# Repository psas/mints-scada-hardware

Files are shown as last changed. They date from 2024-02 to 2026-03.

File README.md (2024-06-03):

# mints-scada-hardware
Minimal Test Stand Supervisory Control and Data Acquisition system hardware and firmware. See [mints-scada-software](https://github.com/psas/mints-scada-software) for the computer software to control the whole system. 

# Assembly
### stm32devboards
* Populate all SMD components on the board
    * Only populate the 60.4 ohm CAN termination resistors on the nodes on the ends of the chain.
    * Populate the USB port and solder its mounting lugs
    * Do not populate the headers on the sides as they will make it more difficult to work on the boards if problems are discovered
* Complete the board testing
* Populate THT components
### interface-module
* Select the desired configuration of the board. This can be one of
    * 8x Push and/or Pull outputs
    * 4x I2C
    * 4x ADC
    * See notes in KiCad for configuration information
* Assemble only the required components for that version of the board. Leave the rest unpopulated

# Firmware flashing
Firmware files are located in the `firmware/bin` directory.

### Command line (recommended)
Command line firmware flashing instructions are provided for Ubuntu 24.04. Other debian-based Linux distros should follow a similar procedure. Flashing from Mac or Windows should be possible, but is not covered here.
#### Setup
1. Install `dfu-util` with `sudo apt install dfu-util`
2. Set up udev rules
    1. Put the following into `/etc/udev/rules.d/60-stm32`
    ```
    # STM32
    ACTION=="add", SUBSYSTEM=="usb", ATTRS{idVendor}=="0483", ATTRS{idProduct}=="df11", TAG+="uaccess"
    ```
    2. Either reboot or run `sudo udevadm control --reload-rules && sudo udevadm trigger` to reload the udev rules

#### Flashing:
1. Remove the devboard from the module if it was installed.
2. Put the device in bootloader mode
    * If the device is unplugged, hold the `BOOT` button while plugging it in
    * If the device is already plugged in, press `RESET` and `BOOT`, then release `RESET` then `BOOT`
3. Run `dfu-util --list` and confirm that there are two devices with the vendor:product ID `0483:df11`, one with the name `@Option Bytes` and one with the name `@Internal Flash`. If any other devices with that ID are present, remove them before continuing.
4. Flash the device with `dfu-util --device 0483:df11 --alt 0 --dfuse-address 0x08000000:leave --download [path/to/file/]<filename>.bin`. It should erase the flash, then download the new file and show `File downloaded successfully` when it is done.

### Visual
[STM32CubeProgrammer](https://www.st.com/en/development-tools/stm32cubeprog.html) can be used to flash device firmware. Setup will be platform-dependent, and thusly not covered here.

To build and upload:
1. Open the PlatformIO tab in the left toolbar
2. Under `PROJECT TASKS` > `Build` > `General` execute the `Build` procedure by clicking on it
3. Execute `Upload` to upload to the microcontroller. Ensure that only a single board is plugged in to ensure you are writing to the correct device.

# Building Firmware
Building firmware from source shouldn't be needed unless you are making changes to it. Firmware build instructions are provided for Ubuntu 24.04. Other debian-based Linux distros should follow a similar procedure. Flashing from Mac or Windows should be possible, but is not covered here.

You will need:
* GCC for arm `sudo apt install gcc-arm-none-eabi`
* make `sudo apt install make`
* Everything as described in the command line flashing setup section above.

To build the code, simply run `make` in the firmware folder. This will build the firmware and copy the .bin into the firmware folder. Running `make flash` will build the firmware then upload it to a connected DFU mode microcontroller.

Initialization code was generated using [https://www.st.com/en/development-tools/stm32cubemx.html](STM32Cube initialization code generator). You should not need to mofidy this, but if you do, the `module_io.ioc` is included. If you regenerate the code, you may have to add
```
#######################################
# Flash
#######################################
flash: all
	dfu-util --device 0483:df11 --alt 0 --dfuse-address 0x08000000:leave --download $(BUILD_DIR)/$(TARGET).bin
```
to the end of `Makefile`. Optionally, add `cp $(BUILD_DIR)/$(TARGET).bin $(TARGET).bin` to target `all` in the makefile (add line 171) to copy the bin out of the build direcotry. Generally, CubeMX does not seem to update the Makefile if it exists.

# Testing
### stm32devboards
1. Populate all SMD components as described in the `assembly` sections. Do not populate THT components yet
2. Visually inspect the board. Fix any issues and inspect again until no issues remain
    * Verify that no pins are shorted
    * Verify the correct orientation and alignment of all components. Pay special attention to the STM32 since its square shape makes it more difficult to notice errors
    * Bridges can hide under the USB port where you can't see them unless you tilt the board to look deep under the port. They can often be fixed by applying flux then heating the two bridged pins.
    * Fixing any of these issues is easier before soldering THT parts since everything here is reflow safe, so it is less likely to be damaged during repairs.
3. Use a DMM to test between `GND` `3v3`, and `GND` and either pad of the polyfuse (the component in the corner of the board by the USB port). Verify there are no shorts.
4. On your computer run `sudo dmesg -Hw` to monitor system messages in real time (`-m`) with human-readable timestamps (`-h`). Keep this window open and visible for the next step
5. Plug the board in via USB. Watch `dmesg`. The following should appear. If it does not, then there is a problem with your board.
```
[<starttime>] usb 3-2: new full-speed USB device number <id> using xhci_hcd
[  +0.148877] usb 3-2: New USB device found, idVendor=0483, idProduct=df11, bcdDevice=22.00
[  +0.000014] usb 3-2: New USB device strings: Mfr=1, Product=2, SerialNumber=3
[  +0.000006] usb 3-2: Product: STM32  BOOTLOADER
[  +0.000006] usb 3-2: Manufacturer: STMicroelectronics
[  +0.000005] usb 3-2: SerialNumber: FFFFFFFEFFFF
```
6. Use the above procedure to flash the `blink-fast.bin` firmware. Confirm that the LED blinks at about 10Hz.
7. Use the above procedure to flash the `blink-slow.bin` firmware. Confirm that the LED blinks at about 1Hz. This confirms that you are able to flash new firmware to the device.
8. Install the THT components as described in the assembly section.

`blink-fast.bin` and `blink-slow.bin` should already be built in the `firmware/bin` directory. If they are not, they can be rebuilt with the blink project. To rebuild them, run the following in `firmware/blink`
```
make clean && make DELAY=500 && cp blink.bin ../bin/blink-slow.bin
make clean && make DELAY=50 && cp blink.bin ../bin/blink-fast.bin
```

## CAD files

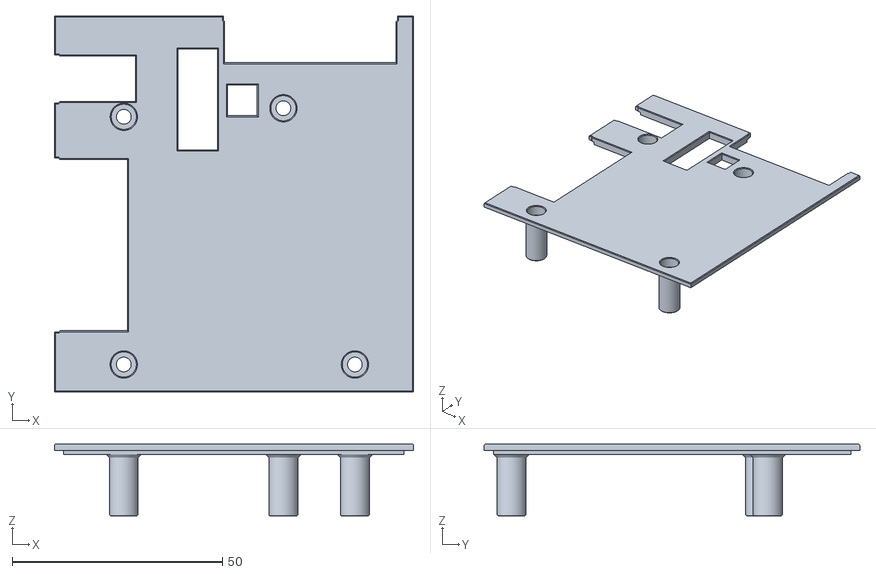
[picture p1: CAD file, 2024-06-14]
interface-module/boxes/minTS Dev Box - Lid - Outputs - v1.7.2.stl
85.5 x 89.5 x 17.1

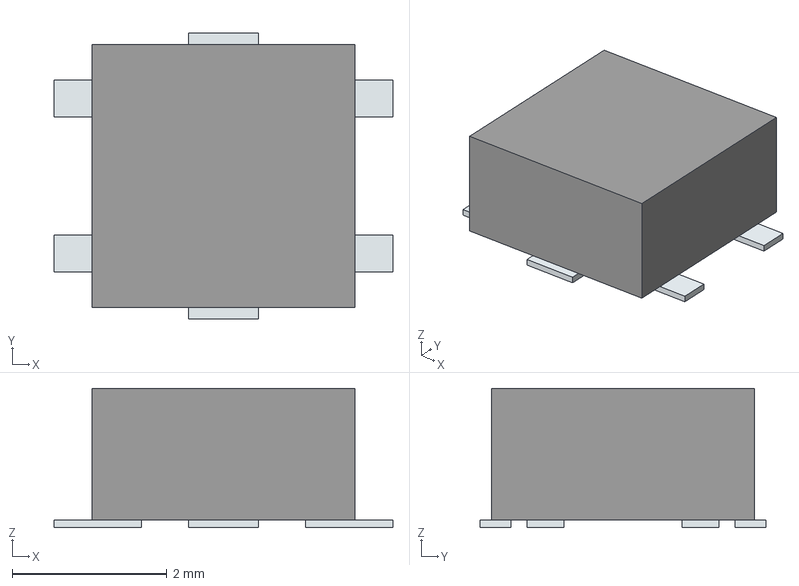
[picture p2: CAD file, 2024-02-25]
stm32devboard/3d/TS21-34-035-BK-260-SMT-TR.stp
4.38 x 3.70 x 1.80 mm
Pins

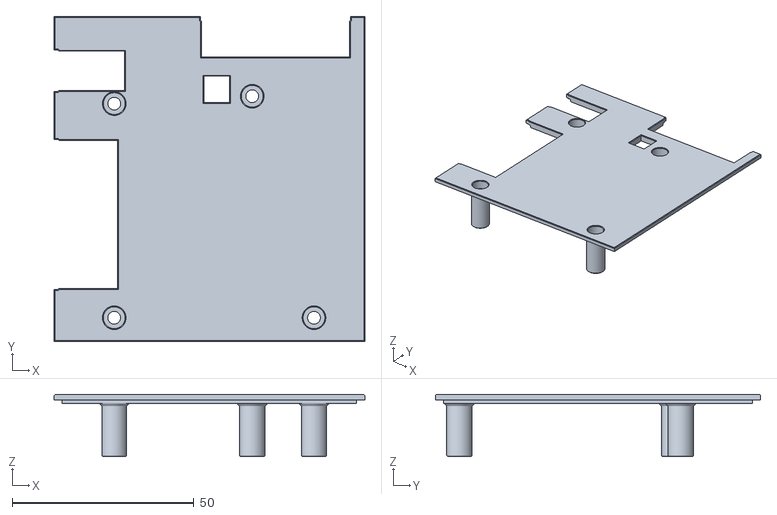
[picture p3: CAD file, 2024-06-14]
interface-module/boxes/minTS Dev Box - Lid - I2C - v1.7.2.stl
85.5 x 89.5 x 17.1

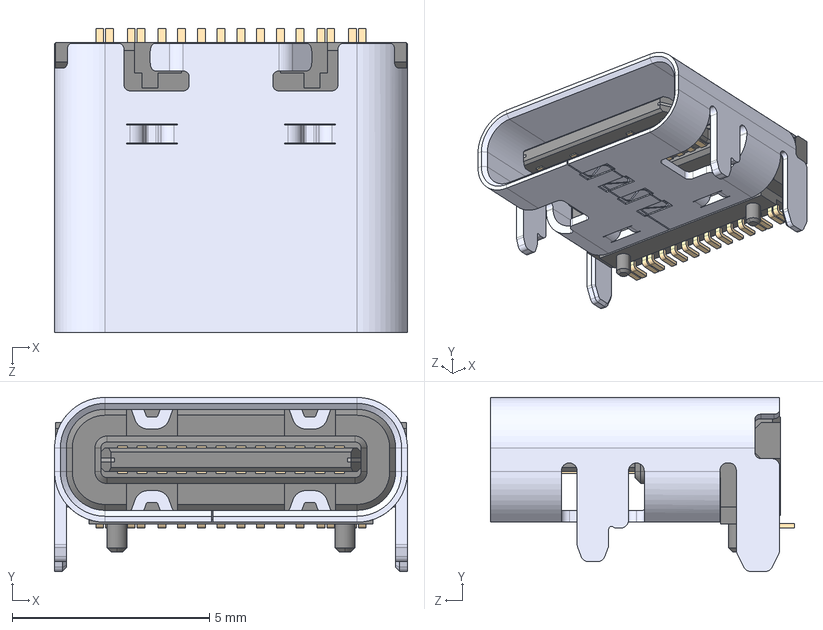
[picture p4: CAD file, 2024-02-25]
stm32devboard/3d/USB4105-GF-A.step
8.94 x 4.41 x 7.71 mm

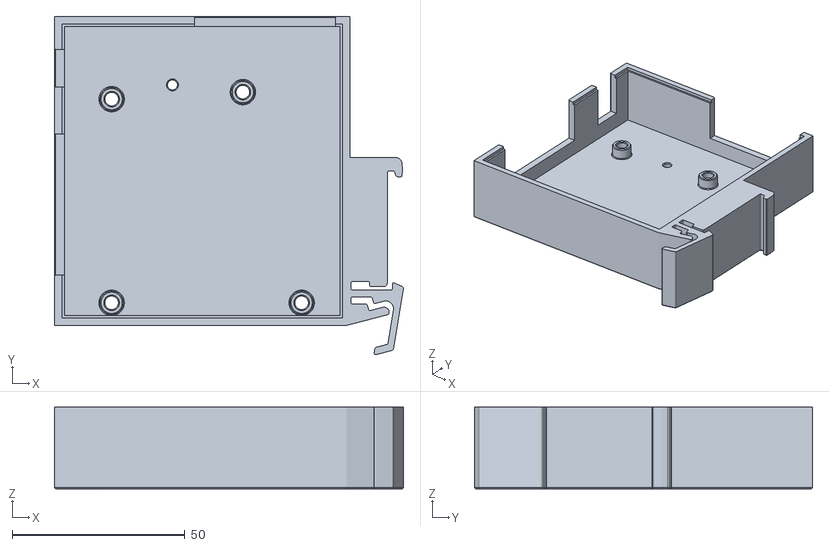
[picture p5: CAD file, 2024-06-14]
interface-module/boxes/minTS Dev Box - Bottom - v1.7.2.stl
101.0 x 97.9 x 23.6

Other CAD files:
interface-module/boxes/minTS Dev Box - Lid - ADC - v1.7.2.stl

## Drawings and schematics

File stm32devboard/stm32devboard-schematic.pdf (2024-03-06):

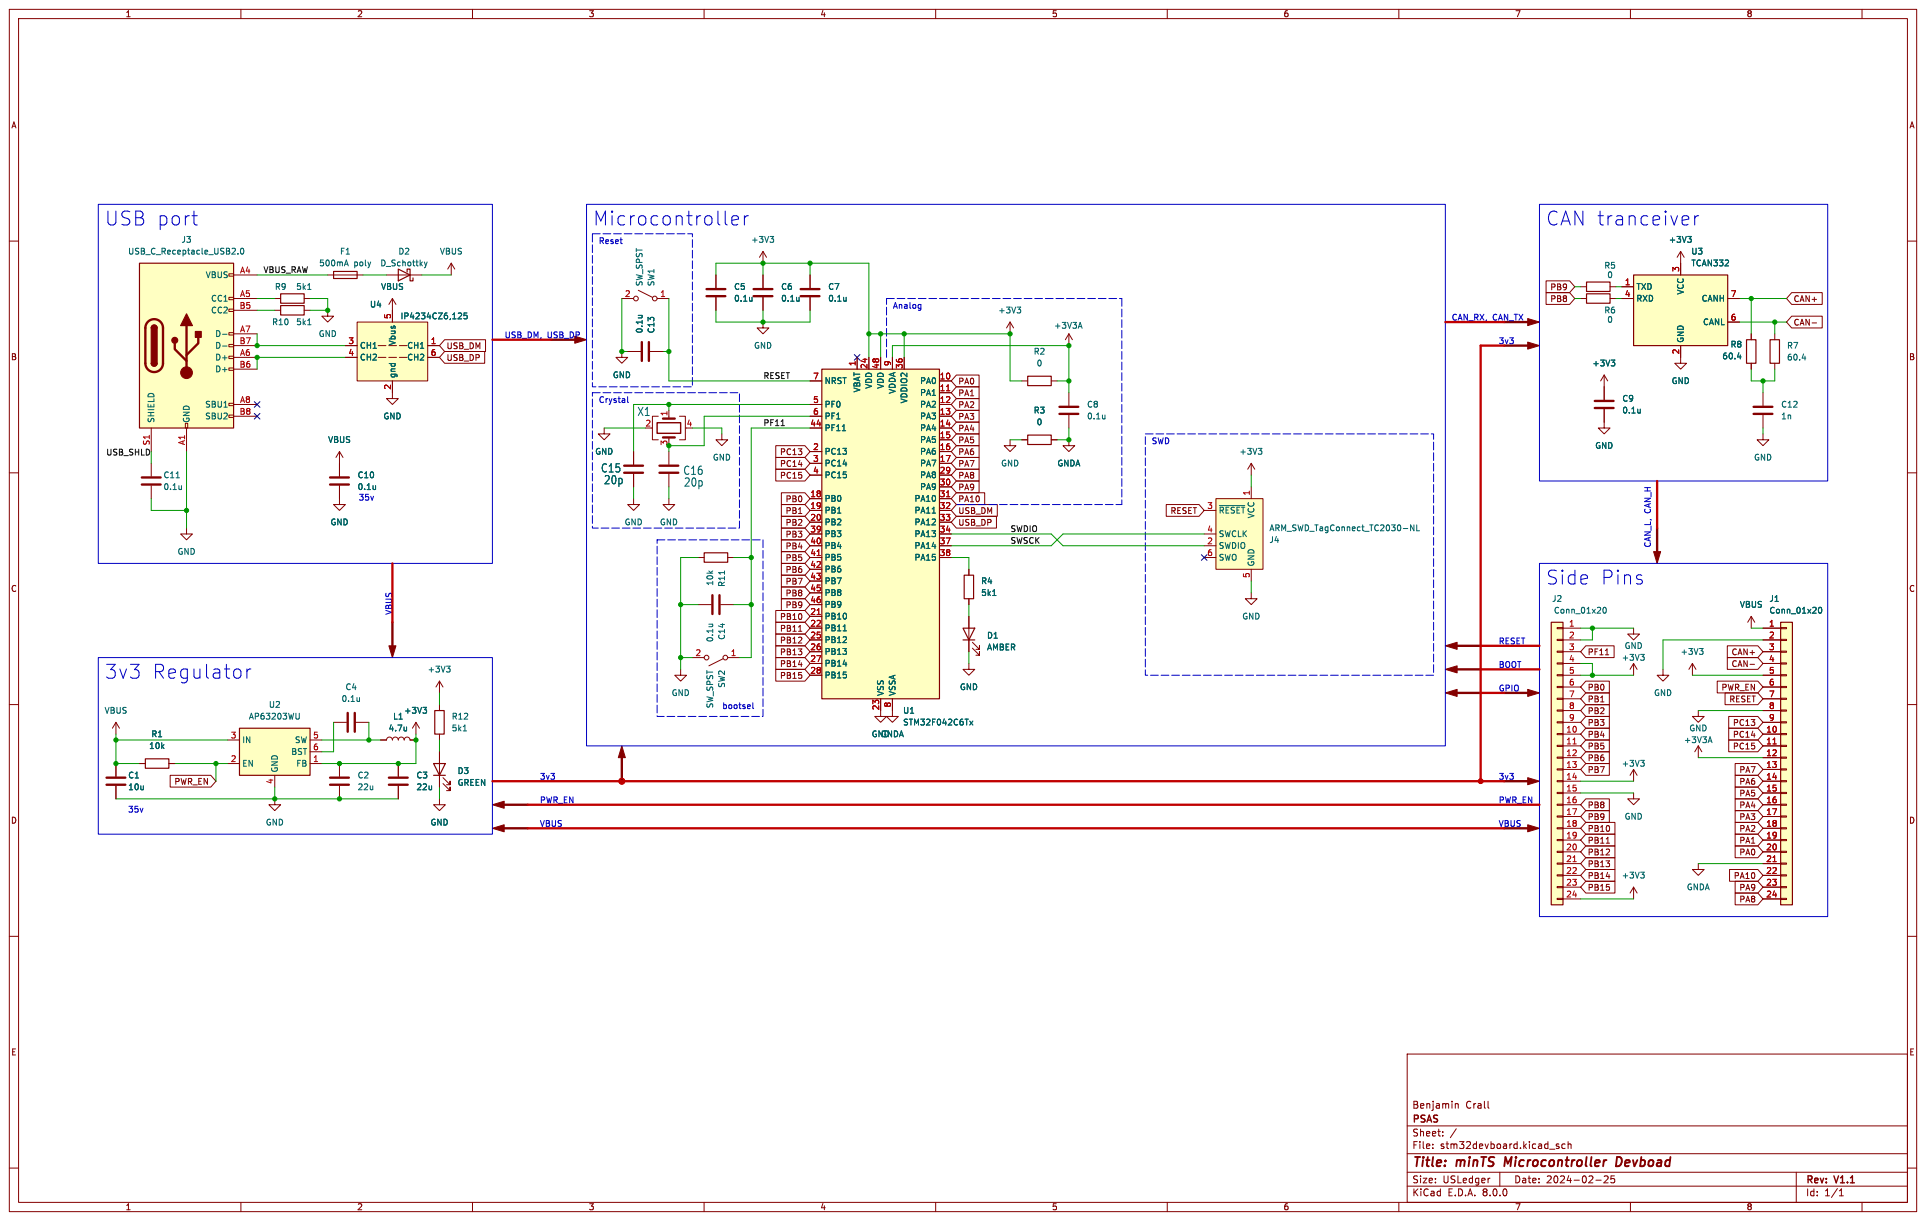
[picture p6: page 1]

1 PA0 10 PA1 11 PA2 12 PA3 13 PA4 14 PA5 15 PA6 16 PA7 17 PB0 18 PB1 19 PC13 2 PB2 20 PB10 21 PB11 22 VSS 23 VDD 24 PB12 25 PB13 26 PB14 27 PB15 28 PA8 29 PC14 3 PA9 30 PA10 31 PA11 32 PA12 33 PA13 34 VDDIO2 36 PA14 37 PA15 38 PB3 39 PC15 4 PB4 40 PB5 41 PB6 42 PB7 43 PF11 44 PB8 45 PB9 46 VDD 48 PF0 5 PF1 6 NRST 7 VSSA

1 SWDIO 2 ~{RESET} 3 SWCLK 4 GND

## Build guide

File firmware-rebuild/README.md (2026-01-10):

Firmware Rebuild

Microcontroller Sub Family: STM32F042X6
Exact Microcontroller: STM32F042C6, 
Footprint: LQFP48

Board Config Template for ./cfg/stm32f0xx_hal_conf.h  comes from
./stm32libs/STM32CubeF0/Drivers/STM32F0xx_HAL_Driver/Inc/stm32f0xx_hal_conf_template.h

Board Config ./cfg/stm32f0xx_hal_conf.h comes from
./stm32libs/STM32CubeF0/Drivers/CMSIS/Device/ST/STM32F0xx/Include/stm32f042x6.h

Board Config Template for ./cfg/usbd_conf.c  comes from
./stm32libs/STM32CubeF0/Middlewares/ST/STM32_USB_Device_Library/Core/Inc/usbd_conf_template.c

Board Config ./cfg/usbd_conf.h comes from
./stm32libs/STM32CubeF0/Middlewares/ST/STM32_USB_Device_Library/Core/Inc/usbd_conf_template.h

Board Config Template for ./cfg/usbd_cdc_if.h comes from
./stm32libs/STM32CubeF0/Middlewares/ST/STM32_USB_Device_Library/Class/CDC/Inc/usbd_cdc_if_template.h

Board Config Template for ./cfg/usbd_cdc_if.c comes from
./stm32libs/STM32CubeF0/Middlewares/ST/STM32_USB_Device_Library/Class/CDC/Src/usbd_cdc_if_template.c

Board Config Template for ./cfg/usbd_desc.c comes from
./stm32libs/STM32CubeF0/Middlewares/ST/STM32_USB_Device_Library/Core/Src/usbd_desc_template.c

Board Config Template for ./cfg/usbd_desc.h comes from
./stm32libs/STM32CubeF0/Middlewares/ST/STM32_USB_Device_Library/Core/Inc/usbd_desc_template.h

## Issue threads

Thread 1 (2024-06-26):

VIN >7.5V kills TVS diode and everything else

Benjamin-C, 2024-06-26:
The VCC pin of the USB TVS diode is connected to VIN, not VIN_USB. This results in it getting way too many volts, probably killing it short, thus killing everything else on the board. This can be fixed by cutting the trace, and rerouting it to after the VIN USB diode.

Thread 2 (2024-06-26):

PFets on interface module are backwards

Benjamin-C, 2024-06-26:
Drain and source on PFets are swapped, resulting in the diode drawing all the power.

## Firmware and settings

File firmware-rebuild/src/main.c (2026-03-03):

#include "main.h"
#include "board_cfg.h"
#include "configuration.h"
#include "can.h"
#include "init.h"
#include "main.h"
#include "stm32f0xx_hal.h"
#include "stm32f0xx_hal_adc.h"
#include "stm32f0xx_hal_gpio.h"
#include "usb.h"

void initPeripherials(void) {
  HAL_Init();
  // Set up clocks
  SystemClock_Config();
  initUSB();
  initGPIO();
  initADC();
  initCAN();
#ifdef CONFIG_I2C
  initI2C1();
#endif
#ifdef CONFIG_ADC
  initSPI();
#endif
}

extern CAN_FilterTypeDef sFilterConfig;
uint8_t baseAddress = 0;

// Represents if a fatal error has occurred

#ifdef LOOPBACK
static int count = 0;
#endif

#ifdef CONFIG_OUTPUTS
GPIO_TypeDef *outputPorts[] = {LED_GPIO_Port,  OUT1_GPIO_Port, OUT2_GPIO_Port,
                               OUT3_GPIO_Port, OUT4_GPIO_Port, OUT5_GPIO_Port,
                               OUT6_GPIO_Port, OUT7_GPIO_Port};
uint16_t outputPins[] = {LED_Pin,  OUT1_Pin, OUT2_Pin, OUT3_Pin,
                         OUT4_Pin, OUT5_Pin, OUT6_Pin, OUT7_Pin};
#endif

#ifdef CONFIG_ADC
#include "mcp346x.h"
MCP346x extadc;
#endif

int fatal = 0;

void onFatalError(void) {
  fatal = 1;
  // Do things here to set things to a safe state.
  // For outputs, this means all off.
  // For inputs, this means nothing.
}

uint32_t random(int bits) {
  uint32_t rsp = 0;
  for (int i = 0; i < bits; i++) {
    HAL_ADC_Start(&hadc);
    while (HAL_ADC_PollForConversion(&hadc, 1000)) {
      // do a little waiting
    }
    rsp <<= 1;
    rsp |= (HAL_ADC_GetValue(&hadc) & 1);
  }
  return rsp;
}

int calc_baseAddress(void) {
  // Read base ID
  baseAddress |= HAL_GPIO_ReadPin(ADDR_GPIO_PORT, ADDR1_Pin) << 4;
  baseAddress |= HAL_GPIO_ReadPin(ADDR_GPIO_PORT, ADDR2_Pin) << 5;
  baseAddress |= HAL_GPIO_ReadPin(ADDR_GPIO_PORT, ADDR4_Pin) << 6;
  baseAddress |= HAL_GPIO_ReadPin(ADDR_GPIO_PORT, ADDR8_Pin) << 7;
  baseAddress += BASE_ADDR_OFFSET;
  return baseAddress;
}

/* Does everything. Is wrapped by main so that the program will halt if this
 * ever returns. */
void doEverything(void) {

  // Initialize ADC
#ifdef CONFIG_ADC
  extadc = MCP346x_Init();
#endif

  // Wait a random amount of time to ensure that if two devices try to start
  // with the same ID, one will have a change to get started and reply to the
  // other alerting them of the issue.
  HAL_Delay(random(6));

  // Read base ID

  uprintf("My base address is 0x%02x\n", baseAddress);

  // Set up the CAN filters
  // Set up a filter. Hopefully it just grabs everything
  CAN_FilterTypeDef sFilterConfig = {
      .FilterFIFOAssignment = CAN_FILTER_FIFO0, // set fifo assignment
      .FilterIdHigh = baseAddress
                      << 5, // the ID that the filter looks for (switch this for
                            // the other microcontroller)
      .FilterIdLow = 0,
      .FilterMaskIdHigh = 0xF0 << 5,
      .FilterMaskIdLow = 0,
      .FilterScale = CAN_FILTERSCALE_32BIT, // set filter scale
      .FilterMode = CAN_FILTERMODE_IDMASK,
      .FilterActivation = ENABLE,
  };

  HAL_StatusTypeDef canSetupStatus = HAL_CAN_ConfigFilter(&hcan, &sFilterConfig);
  if (canSetupStatus != HAL_OK) {
    uprintf("CAN filter init Error %d\n", canSetupStatus);
    onFatalError();
    return;
  } else {
    uprintf("CAN filter initalized\n");
  }
  // Start CAN and alert if it failed
  canSetupStatus = HAL_CAN_Start(&hcan);
  if (canSetupStatus != HAL_OK) {
    uprintf("CAN start error %d\n", canSetupStatus);
    onFatalError();
    return;
  } else {
    uprintf("CAN started\n");
  }

  // Setup ID claim command
  struct DataPacket_t iddp = {
      .id = baseAddress,
      .err = 0, // Not an error packet
      .reserved = 0,
      .reply = 0,                  // Not a reply
      .data.seq = 0,               // Don't care what it is
      .data.cmd = BUSCMD_CLAIM_ID, // Sets the ID to claim
      .datasize = 8, // Include the sequence number and command in this count
  };
  compressUID(iddp.data.bytes);
  // Send ID claim command
  int freeTX = HAL_CAN_GetTxMailboxesFreeLevel(&hcan);
  int ts = writeDatapacketToCan(&iddp);
  if (ts != HAL_OK) {
    uprintf("\n[FATAL] Could not send CAN address claim packet.");
    onFatalError();
    return;
  }
  uprintf("Sent ID query ");
  printDataPacket(&iddp);
  uprintf("\n");
  // Wait for ID claim command to be sent
  while (HAL_CAN_GetTxMailboxesFreeLevel(&hcan) < freeTX);

  while (1) {
    getCanMessages();
#ifdef LOOPBACK
    DataPacket dp;
    // dp.id = 0x75;
    // dp.id = count & 0xFF;
    dp.id = baseAddress | 0x5;
    dp.err = 0;                        // Not an error packet
    dp.reserved = 0;                   // Set to 0 for easier debugging
    dp.reply = 0;                      // Not a reply
    dp.data.seq = count & 0xFF;        // Increment sequence number each time
    dp.data.cmd = BUSCMD_READ_ID_HIGH; // Sets the ID to claim
    dp.data.bytes[0] = 0x00;
    dp.data.bytes[1] = 0x01;
    dp.data.bytes[2] = 0x02;
    dp.data.bytes[3] = 0x03;
    dp.datasize = 6; // Include the sequence number and command in this count

    uint32_t endtime = HAL_GetTick() + 500;
    HAL_GPIO_WritePin(LED_GPIO_Port, LED_Pin, GPIO_PIN_SET);
    uprintf("0x%x Test TX %4d", random(4), count++);
    int ts = writeDatapacketToCan(&dp);
    uprintf("[%d]: ", ts);
    printDataPacket(&dp);
    uprintf("\n");
    HAL_Delay(50);
    HAL_GPIO_WritePin(LED_GPIO_Port, LED_Pin, GPIO_PIN_RESET);
    while (endtime > HAL_GetTick()) {
      // HAL_Delay(1);
    }
#endif
  }
}

int main(void) {
  // Initialize peripherial libraries
  initPeripherials();

  // Wait a moment for USB to connect
  // Might disable for production
  HAL_Delay(2000);
  uprintf("Hello\n");

  doEverything();
  while (1); // Halt if main ever exits
}

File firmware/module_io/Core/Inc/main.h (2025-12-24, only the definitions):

#define CONFIG0_Pin GPIO_PIN_0
#define CONFIG0_GPIO_Port GPIOA
#define CONFIG1_Pin GPIO_PIN_1
#define CONFIG1_GPIO_Port GPIOA
#define ADC_RAND_Pin GPIO_PIN_2
#define ADC_RAND_GPIO_Port GPIOA
#define ADDR4_Pin GPIO_PIN_4
#define ADDR4_GPIO_Port GPIOA
#define ADDR1_Pin GPIO_PIN_5
#define ADDR1_GPIO_Port GPIOA
#define ADDR8_Pin GPIO_PIN_6
#define ADDR8_GPIO_Port GPIOA
#define ADDR2_Pin GPIO_PIN_7
#define ADDR2_GPIO_Port GPIOA
#define OUT0_Pin GPIO_PIN_0
#define OUT0_GPIO_Port GPIOB
#define OUT1_Pin GPIO_PIN_1
#define OUT1_GPIO_Port GPIOB
#define OUT2_Pin GPIO_PIN_2
#define OUT2_GPIO_Port GPIOB
#define CTRL_Pin GPIO_PIN_12
#define CTRL_GPIO_Port GPIOB
#define LED_Pin GPIO_PIN_15
#define LED_GPIO_Port GPIOA
#define OUT3_Pin GPIO_PIN_3
#define OUT3_GPIO_Port GPIOB
#define OUT4_Pin GPIO_PIN_4
#define OUT4_GPIO_Port GPIOB
#define OUT5_Pin GPIO_PIN_5
#define OUT5_GPIO_Port GPIOB
#define OUT6_Pin GPIO_PIN_6
#define OUT6_GPIO_Port GPIOB
#define OUT7_Pin GPIO_PIN_7
#define OUT7_GPIO_Port GPIOB

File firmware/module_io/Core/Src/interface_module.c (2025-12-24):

// Hardware setup functions config
// USB setup functions
// #include "usb_device.h"
// DataPackets
#include "interface_module.h"

#include "stm32f042x6.h"
#include "stm32f0xx_hal.h"
#include "stm32f0xx_hal_can.h"
#include "stm32f0xx_hal_adc.h"
#include "main.h"
#include "uprintf.h"
#include "buscommands.h"
#include "configuration.h"

#include "datapacket.h"

// #include "loop.h"

/** TODO
 * Add checkbox to software in order to quickly remove sensors from the autopoller
 * Add message queue to firmware so that long tasks don't block future messages.
 */

extern CAN_FilterTypeDef sFilterConfig;
uint8_t baseAddress = 0;

// Represents if a fatal error has occurred
int fatal = 0;

#ifdef LOOPBACK
static int count = 0;
#endif

#ifdef CONFIG_OUTPUTS
GPIO_TypeDef* outputPorts[] = {LED_GPIO_Port, OUT1_GPIO_Port, OUT2_GPIO_Port, OUT3_GPIO_Port, OUT4_GPIO_Port, OUT5_GPIO_Port, OUT6_GPIO_Port, OUT7_GPIO_Port};
uint16_t outputPins[] = {LED_Pin, OUT1_Pin, OUT2_Pin, OUT3_Pin, OUT4_Pin, OUT5_Pin, OUT6_Pin, OUT7_Pin};
#endif

#ifdef CONFIG_ADC
#include "mcp346x.h"
MCP346x extadc;
#endif

void onFatalError(void) {
    fatal = 1;
    // Do things here to set things to a safe state.
    // For outputs, this means all off.
    // For inputs, this means nothing.
}

/**
 * Copies several bytes of UID to somewhere
 * Copies 0 < bytes <= 12 bytes to dest
 * Starts at 0 <= offset < 12 bytes into the UID
 * If bytes of offset would give illegal locations, they are modified to not.
*/
void copyUID(uint8_t* dest, uint8_t bytes, uint8_t offset) {
    if(offset > 11) {
        offset = 11;
    }
    if(bytes + offset > 12) {
        bytes = 12 - offset;
    }
    if(bytes < 1) {
        bytes = 1;
    }

    // UID_BASE
    uint8_t* rdp = (uint8_t*) (UID_BASE + offset);
    for(int i = 0; i < bytes; i++) {
        *dest++ = *rdp++;
    }
}

/**
 * Writes a compressed version of the UID to a given memory location.
 * Always writes 6 bytes
*/
void compressUID(uint8_t* dest) {
    uint8_t* uid = (uint8_t*) UID_BASE;

    for(int i = 0; i < 6; i++) {
        dest[i] = (uid[i] + uid[i+6]) & 0xFF;
    }
}

int processPacket(DataPacket* pk) {
    uint8_t subid = (pk->id & 0xF) - BASE_ADDR_OFFSET;
    uprintf("#%d ", subid);

    // If the packet was an error, check if it's one we care about
    if(pk->err) {
        uprintf("That was an error message!");
        // If soneone else said they have my ID, that's bad and we need to stop.
        if(pk->data.cmd == BUSCMD_CLAIM_ID) {
            uint8_t tempid[6];
            compressUID(tempid);
            int f = 0;
            for(int i = 0; i < 6; i++) {
                f &= tempid[i] != pk->data.bytes[i]; 
            }
            if(f) {
                onFatalError();
                uprintf("\n[FATAL] Someone else already had my ID %02x\n", baseAddress);
            }
        }
        return 1;
    }
    // If the packet was a reply, then someone else is using my ID.
    // This is not allowed, so send an error reply

    // If the packet is a reply, it was probably just sent by us, so ignore it.
    if(pk->reply) {
        // onFatalError();
        // uprintf("[FATAL] Someone else with my ID sent a reply");
        // pk->err = 0; // Don't set the error bit 
        // pk->reply = 1;
        // writeDatapacketToCan(pk);
        // return 2;
        uprintf("That was a reply.");
        return 0;
    }
    if(pk->datasize < 2) {
        uprintf("Command too short!");
        return 3;
    }
    uprintf("Exec time! ");
    switch(pk->data.cmd) {
    case BUSCMD_CLAIM_ID: {
        uprintf("Id claim commnd!");
        uint8_t tempid[6];
        compressUID(tempid);
        int f = 0;
        for(int i = 0; i < 6; i++) {
            f &= tempid[i] != pk->data.bytes[i]; 
        }
        if(f) {
            pk->err = 1;
            pk->reply = 1;
            writeDatapacketToCan(pk);
        } else {
            uprintf("It was me");
        }
    } break;
    case BUSCMD_READ_ID_LOW: {
        uprintf("UID low read");
        pk->reply = 1;
        pk->datasize = 8;
        copyUID(pk->data.bytes, 6, 0);
    } break;
    case BUSCMD_READ_ID_HIGH: {
        uprintf("UID low high");
        pk->reply = 1;
        pk->datasize = 8;
        copyUID(pk->data.bytes, 6, 6);
        writeDatapacketToCan(pk);
    } break;
#ifdef CONFIG_OUTPUTS
    case BUSCMD_READ_VALUE: {
        uprintf("Read value command");
        uint32_t val = HAL_GPIO_ReadPin(outputPorts[subid], outputPins[subid]);
        pk->datasize = 8;
        // BigLittleData* bld = BIGLITTLEDATA(pk);
        BIGLITTLEDATA(pk)->big = val;
        // bld->big = val;
        pk->reply = 1;
        uprintf("\nSending reply ");
        printDataPacket(pk);
        writeDatapacketToCan(pk);
    } break;
    case BUSCMD_WRITE_VALUE: {
        uprintf("Write value command");
        HAL_GPIO_WritePin(outputPorts[subid], outputPins[subid], BIGLITTLEDATA(pk)->big);
    } break;
#endif
#ifdef CONFIG_ADC
    case BUSCMD_READ_VALUE: {
        uprintf("Read value command. %d %d", subid << 1, (subid << 1) + 1);
        // uint32_t val = MCP346x_analogRead(&extadc, MUX_AVDD, MUX_AGND, GAIN_1);
        uint32_t val = MCP346x_analogRead(&extadc, subid << 1, subid << 1 + 1, GAIN_1);
        pk->datasize = 8;
        // BigLittleData* bld = BIGLITTLEDATA(pk);
        BIGLITTLEDATA(pk)->big = val;
        // bld->big = val;
        pk->reply = 1;
        uprintf("\nSending reply ");
        printDataPacket(pk);
        writeDatapacketToCan(pk);
    } break;
#endif
    default: {
        uprintf("Unknown command");
    }
    }
    return 0;
}

void getCanMessages(void) {
    while(!fatal && HAL_CAN_GetRxFifoFillLevel(&hcan, CAN_RX_FIFO0)) {
        HAL_GPIO_WritePin(LED_GPIO_Port, LED_Pin, GPIO_PIN_SET);
        uprintf("Got message! ");
        DataPacket pk;
        pk.id = 0;
        pk.err = 0;
        pk.reply = 0;
        pk.data.seq = 0;
        pk.data.cmd = 0;
        for(int i = 0; i < 6; i++) {
            pk.data.bytes[i] = 0;
        }
        pk.datasize = 0;
        int rs = readDataPacketFromCan(&pk);
        if(rs != DATAPACKET_READ_SUCCESS) {
            uprintf("Packet read fail! %d\n", rs);
            return;
        }
        printDataPacket(&pk);

        uint8_t bid = pk.id & 0xF0;
        uprintf(" BID:%2x", bid);

        if((pk.id & (0xF0 | SUB_ADDR_MASK)) == baseAddress) {
            uprintf(" 4Me!");

            processPacket(&pk);
        }

        uprintf("\n");
        HAL_GPIO_WritePin(LED_GPIO_Port, LED_Pin, GPIO_PIN_RESET);
    }
}

uint32_t random(int bits) {
    uint32_t rsp = 0;
    for(int i = 0; i < bits; i++) {
        HAL_ADC_Start(&hadc);
        while(HAL_ADC_PollForConversion(&hadc, 1000)) {
            // do a little waiting
        }
        rsp <<= 1;
        rsp |= (HAL_ADC_GetValue(&hadc) & 1);
    }
    return rsp;
}
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

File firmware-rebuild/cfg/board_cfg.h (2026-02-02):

// // Configuration: Select exactly one. Selecting multiple may lead to issues
// #define CONFIG_OUTPUTS
// // #define CONFIG_ADC
// // #define CONFIG_I2C
//
// // Check that exactly 1 output configuration has been selected
// #if !(defined(CONFIG_OUTPUTS) || (defined(CONFIG_ADC) ||
// defined(CONFIG_I2C))) \
//     || (defined(CONFIG_OUTPUTS) && (defined(CONFIG_ADC) ||
//     defined(CONFIG_I2C))) \
//     || (defined(CONFIG_ADC) && defined(CONFIG_I2C))
//     #error("You must specify exactly 1 of CONFIG_OUTPUTS, CONFIG_ADC, or
//     CONFIG_I2C")
// #endif
//
// #ifdef CONFIG_OUTPUTS
// #define BASE_ADDR_OFFSET 0
// #endif
// #ifdef CONFIG_ADC
// #define BASE_ADDR_OFFSET 8
// #endif
// #ifdef CONFIG_I2C
// #define BASE_ADDR_OFFSET 12
// #endif
// testing use

void SystemClock_Config(void);
#define BASE_ADDR_OFFSET 12

// Pin definitions //

// PA is in GPIOA & PB is in GPIOB
// See PCB layout as to why they are ordered in this manner

#define ADDR4_Pin GPIO_PIN_4
#define ADDR1_Pin GPIO_PIN_5
#define ADDR8_Pin GPIO_PIN_6
#define ADDR2_Pin GPIO_PIN_7
#define ADDR_GPIO_PORT GPIOA

#define LED_Pin GPIO_PIN_15
#define LED_GPIO_Port GPIOA

#define SPI_PORT GPIOB
#define SPI_CS GPIO_PIN_12
#define SPI_SCK GPIO_PIN_13
#define SPI_MISO GPIO_PIN_14
#define SPI_MOSI GPIO_PIN_15

#define CONFIG0_Pin GPIO_PIN_0
#define CONFIG0_GPIO_Port GPIOA
#define CONFIG1_Pin GPIO_PIN_1
#define CONFIG1_GPIO_Port GPIOA

#define ADC_RAND_Pin GPIO_PIN_2
#define ADC_RAND_GPIO_Port GPIOA

#define OUT0_Pin GPIO_PIN_0
#define OUT0_GPIO_Port GPIOB
#define OUT1_Pin GPIO_PIN_1
#define OUT1_GPIO_Port GPIOB
#define OUT2_Pin GPIO_PIN_2
#define OUT2_GPIO_Port GPIOB

#define CTRL_Pin GPIO_PIN_12
#define CTRL_GPIO_Port GPIOB

#define OUT3_Pin GPIO_PIN_3
#define OUT3_GPIO_Port GPIOB
#define OUT4_Pin GPIO_PIN_4
#define OUT4_GPIO_Port GPIOB
#define OUT5_Pin GPIO_PIN_5
#define OUT5_GPIO_Port GPIOB
#define OUT6_Pin GPIO_PIN_6
#define OUT6_GPIO_Port GPIOB
#define OUT7_Pin GPIO_PIN_7
#define OUT7_GPIO_Port GPIOB

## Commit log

2024-02-25 Added stm32u042 and CAN dev board
    [TS21-34-035-BK-260-SMT-TR.stp, USB4105-GF-A.step, stm32devboard.kicad_pcb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]
2024-03-05 Fixed DR fixes
    [stm32devboard.kicad_pcb, stm32devboard.kicad_sch]
2024-03-06 Updated BOM and silkscreen
    [stm32devboard.kicad_pcb, stm32devboard.kicad_sch]
2024-03-06 Created schematic and layout PDFs
2024-03-12 Fixed issues from DR
    [stm32devboard.kicad_pcb]
2024-03-12 Added title silkscreen
    [stm32devboard.kicad_pcb]
2024-04-24 Created iBom
    [stm32devboard.kicad_sch]
2024-05-02 Fixed boot button and updated silkscreen
    [stm32devboard.kicad_pcb, stm32devboard.kicad_sch]
2024-05-03 Added interface module
    [interface-module.kicad_pcb, interface-module.kicad_sch, outputs.kicad_sch]
2024-05-03 Fixed footprints
    [interface-module.kicad_pcb, interface-module.kicad_sch, outputs.kicad_sch]
2024-05-05 routed most of board
    [interface-module.kicad_pcb, interface-module.kicad_sch, outputs.kicad_sch]
2024-05-05 Finished copper layout
    [interface-module.kicad_pcb, interface-module.kicad_sch, outputs.kicad_sch]
2024-05-05 Updated silkscreen
    [config1_adc.kicad_sch, config2_outputs.kicad_sch, config3_i2c.kicad_sch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]
2024-05-05 Exported devboard STEP
    [config1_adc.kicad_sch, interface-module.kicad_pcb, stm32devboard.kicad_pcb]
2024-05-05 More silkscreen and fixing some footprints
    [config1_adc.kicad_sch, interface-module.kicad_pcb, interface-module.kicad_sch]
2024-05-05 Added ADC biasing resistor
    [config1_adc.kicad_sch, config2_outputs.kicad_sch, config3_i2c.kicad_sch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]
2024-05-05 Fixed output polarity
    [config2_outputs.kicad_sch, interface-module.kicad_pcb]
2024-05-05 Added LEDs for outputs and improved silkscreen
    [config1_adc.kicad_sch, config2_outputs.kicad_sch, config3_i2c.kicad_sch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]
2024-05-05 Moved aux power silkscreen
    [interface-module.kicad_pcb]
2024-05-06 Fixed hole plating issue
    [stm32devboard.kicad_pcb]
2024-05-06 Updated all kicad projects with build directory and plotting options, and added .gitignore to ignore standard build products.
    [interface-module.kicad_pcb, stm32devboard.kicad_pcb]
2024-05-08 Fixed BOM issues
    [config1_adc.kicad_sch, config2_outputs.kicad_sch, config3_i2c.kicad_sch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]
2024-05-27 Prep for assembally
    [TS21-34-035-BK-260-SMT-TR.stp, USB4105-GF-A.step, config1_adc.kicad_sch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]
2024-05-28 Switched to Makefile-based build
2024-05-28 Added USB printf function
2024-06-02 got basic DataPacket framework working
2024-06-03 It now talks to software
    [configuration.h]
2024-06-03 Fixed data format bugs
    [configuration.h]
2024-06-03 Added address pin labels
    [interface-module.kicad_pcb, interface-module.kicad_sch]
2024-06-14 Added box STLs
    [minTS Dev Box - Bottom - v1.7.2.stl, minTS Dev Box - Lid - ADC - v1.7.2.stl, minTS Dev Box - Lid - I2C - v1.7.2.stl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]
2025-12-22 Start firmware rebuild and reorganization
    Won't rebuild 100% from scratch, will use original firmware as a
    reference and copy things as needed/wanted.
    [main.c]
2025-12-22 initial MCP3464 implementation
    [configuration.h]
2025-12-22 Change submodule to STM32CubeF0 and start code org STM32CubeF0 has the recursive submodules for the HAL and CMSIS.
2025-12-23 Setup init, gpio pins detection, and blinky test
    Copied Ben's system clock configuration, uprint functions, and some
    other ideas over. Now in a state to start flashing boards, debugging and
    implementing from there. Still Some issues within the Makefile that still need
    to be sorted out.
    [board_cfg.c, board_cfg.h, init.c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]
2025-12-23 Revision, updated diodes and transistors
    Moved to a more robust transistor arrangement with a new zener diode
    [config1_adc.kicad_sch, config2_outputs.kicad_sch, config3_i2c.kicad_sch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]
2025-12-23 Fixed transistor tracing
    [config2_outputs.kicad_sch, interface-module.kicad_pcb]
2025-12-23 Updated with better traces
    [interface-module.kicad_pcb]
2025-12-23 Better vpow contact
    [interface-module.kicad_pcb]
2025-12-24 Ready for more scrutiny
    [interface-module.kicad_pcb]
2025-12-24 Better via placement and updated filled zones
    [interface-module.kicad_pcb]
2025-12-24 Upgraded to v1.1.
    [config1_adc.kicad_sch, config2_outputs.kicad_sch, config3_i2c.kicad_sch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]
2025-12-24 Clean up DRC violations
    [interface-module.kicad_pcb]
2025-12-24 Fix git stashing errors and Makefile
    [main.c, main.h]
2025-12-25 WIP: Improving Makefile and added missing configs
    Still in the process of fixing the build system. Running into a lot of
    weird errors with multiple definitions in object files once I "fixed" STM32 drivers (see
    README changes in the firmware-rebuild directory). As well as memory
    region errors which I suspect to be from misconfiguration of either the
    MCU configs or the way I am building.
    [board_cfg.c]
2025-12-25 Final polish before manufacturing (v1.1)
    Upped version to 1.1. Cleared ERC errors, one interesting one left that won't stop manufacturing. Cleared all DRC warnings and
    errors. Formatted BOM. Fixed BOM for important parts. Added fuse parts for reference. Cleaned up silkscreen.
    [config1_adc.kicad_sch, config2_outputs.kicad_sch, config3_i2c.kicad_sch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]
2025-12-25 WIP: CAN and build system improvements
    Started some work on initial CAN implementation and experimented with
    the Makefile. Copying what was done in Ben's generated Makefile, and
    seeing what was needed I got further along due to the `--gc-sections` flag.
    However, it still needs those STM library temp fixes.
    [can.c, main.c, main.h]
2025-12-25 Fix submodules and accidental code overwrite
    Got rid of the unnecessary submodule since it is recursively added
    by STM32CubeF0 submodules. Early commit overwrote some of Ben's code
    reverted the file to match how it previously was.
2025-12-26 Changed configs to fix build errors
    Previously mentioned changes to STMs code in order to remove the build
    errors in the README are now undone. Issues stemmed from the configs not
    having the PCD module enabled and including the HAL header file. Also
    got rid of the seemingly useless gcc flag, `-specs=nano.specs` that I
    took from the older code. No documentation exists for that flag so idk
    what it does.
    [main.c]
2025-12-28 Fix Naming and small syntax errors
    Building fine now. Major blocker is USB, following the
    README on running dmesg, we get errors of "Device not responding to
    setup address".
    [can.c, init.c, main.c]
2025-12-31 Fix for TVS diode to be set to <=5V
    [stm32devboard.kicad_pcb, stm32devboard.kicad_sch]
2026-01-02 Clarify footprint and openocd
    [oocd.cfg]
2026-01-04 Start wiring-diagram of minTS in KiCAD
    [wiring-diagram.kicad_pcb, wiring-diagram.kicad_sch]
2026-01-10 Add interrupt and exception handler functions
    Most importantly the function `SysTick_Handler()` was added that then
    calls `HAL_IncTick()`. The function needs to be defined since it is
    included in the vector table of `startup_stm32f042x6.s`.
2026-01-11 Started initial work on CAN and ADC
    Using the initial code as a reference slowly going through and
    reimplementing things.
2026-01-31 index on main: 13efbac Started initial work on CAN and ADC
2026-02-02 Move focus just onto ADC implementation & repo org
    After some consideration I thought it might be best to just focus on
    implementing wait is needed for the next fire. Then later on possibly work on
    better ways to reimplement parts of the firmware.
    [configuration.h]
2026-02-05 Fix up build errors and organize remaining defs
    A lot of reorganizations and placing definitions outside of function
    calls. The MCP346x struct `adc` is not being seen when used as an argument for
    `MCP346x_analogRead()` at the moment. Will need to be fixed to be ready
    for testing
    [configuration.h]
2026-02-19 added VBUS label
    [stm32devboard.kicad_pcb]
2026-02-21 Updated schematic and board to fab run of v1.3 on 2026-01-27.
    [stm32devboard.kicad_pcb, stm32devboard.kicad_sch]
2026-02-21 fix includes for spi
    [can.c, mcp346x.c, mcp346x.h]
2026-03-01 misc fixes + cleanup
    [can.c, init.c, main.c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]
2026-03-01 remove old misleading comment
    [oocd.cfg]
2026-03-01 remove dnp attributes for different variants
    [config1_adc.kicad_sch, config3_i2c.kicad_sch]
2026-03-03 Change to 32-bit spi readings
    [configuration.h]

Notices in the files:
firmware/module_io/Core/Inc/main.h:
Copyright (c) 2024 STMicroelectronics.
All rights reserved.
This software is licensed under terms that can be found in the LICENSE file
